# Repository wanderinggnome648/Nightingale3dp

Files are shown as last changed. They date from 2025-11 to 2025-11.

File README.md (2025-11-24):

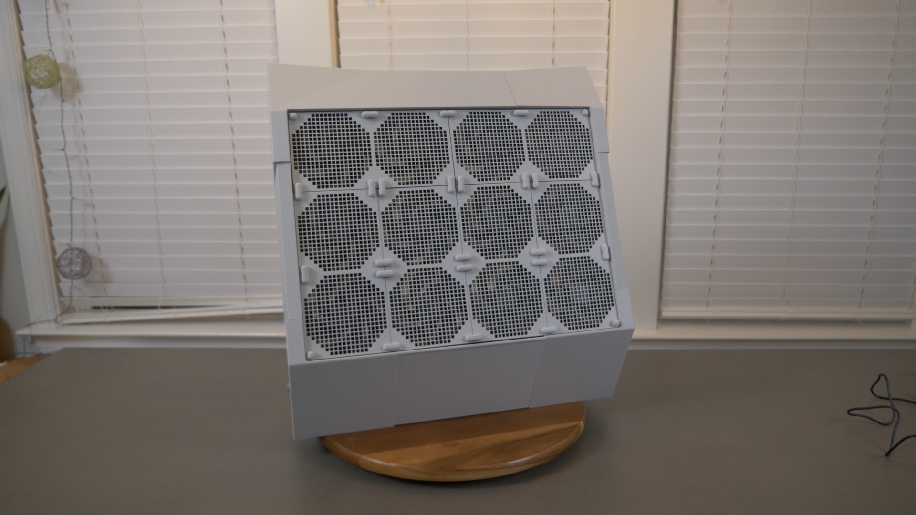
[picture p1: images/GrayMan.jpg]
Product image


# The Nightingale 3DP: An Open-Source, 3D Printed, Ultra-Quiet, Effective Air Purifier With Low Maintenance Costs

A PC-fan based air purifier design, the Nightingale's major features are:  
- **3D Printed**: Most parts are 3D printed, including the air purifier housing, fan grills, and connectors. You only need a filter, super glue, some wiring, and an A/C adapter.
- **Effective**: Purifies air with one 20x20x5 MERV 13 air filter is efficient at removing pollen, dust, and infectious aerosols, but have very high air flow.  
- **Ultra-Quiet**: No need to turn it down or off due to noise because you'll barely know it's running. Uses PC fans designed to push a high volume of air quietly. 
- **Easy Filter Change**: When you change the filters simply open the lid and replace. No disassembly required.
- **Cheap Maintenance**: No pricey filter replacement costs. Simply use standard MERV 13, 20x20x5 furnace filters commonly available in the US at $35-$40. Change yearly or after wildfire events. 
- **Open-Source**: No vendor lock-in. Build it. It's yours. If you have a problem, fix it. 
- **Low Energy Consumption** Consumes only enough electricity for 12 PC fans. 
- **Slim Design**: About the size of a desktop computer, it doesn't take up much space. Sit against the wall, and due to the angled design, it will still have good airflow. Air flow angles up slighty to help room mixing. 
- **Easy Wiring**: Uses standard connectors interior connectors (DC) that plug together. No soldering required.  

# Release Notes

## Version 1 - Baseline
Released on Nov 24, 2025. 

## 3D Printed Components
- Print all the items in the Nightingale_3d_7percent.3mf file with 2 Wall Loops, 7% Gyroid fill (to save on filament)
- Print all the items in the Nightingale_3d_30percent.3mf file with 2 Wall Loops, 30% Gyroid fill (for additional strength)
- You should be able to print all components with less then 3 rolls of filament. 
- You need cable ties for the wiring and those can also be printed. 

## Parts to Buy
| Quantity | Item | Description | Cost | Link  |
| --- | -----| --- | ---- | ----- |
| 1 | DC Barrel Jack | Used to easily connect to ac/dc adapter | $8 | 
| 1 | 12 volt, 4 amp AC/DC Adapter | Power source | $10 | [LINK](https://www.amazon.com/Converter-100-220V-Transformer-5-5x2-1mm-Accessories/dp/B08C594VNP/?th=1)
| 1 | 3 Way PWM Splitter | The splits 1 cable into 3 | $3 | [LINK](https://www.amazon.com/Splitter-Converter-Extension-Splitters-Computer/dp/B0DS2CVYZJ) (3-pack)
| 2 | 5-Port PWM Hubs | This connects multiple fans to power | $13 | [LINK](https://www.amazon.com/dp/B0CY521W9R/)
| 12 | P12 (120mm) PC Fans | Ideally, fluid bearings and advertised as quiet, Artic P12 is a solid inexpensive options | $68 | 2x [LINK](https://www.amazon.com/dp/B07HC7P3HJ/), 2x [LINK](https://www.amazon.com/ARCTIC-P12-120-Pressure-optimised-Quiet-Computer/dp/B07GB16RK7)
| 1 | MERV 13 20x20x5 Furnace Filter | Main filter for the unit | $45 | [LINK](https://www.nordicpure.com/product/20x20x5-air-filter/ ) |

Note: 20x20 furnace filters are NOT 20" long. They are always a little smaller. I designed this purifier to fit a filter with NordicPure sizing and some additional space for variances. 

## Other Parts and Tools
- Screwdriver - Connecting the fans to the panels
- Rubber mallet - Helps get stuff to fit snugly w/o damaging it
- Wood Glue - For affixing the filter holders
- Utility knife - Cutting zip ties, opening packages
- Cable ties - Organizing the wiring

# Assembly
[AssemblyVideo](https://youtu.be/DHxAwtPqRJc)

## Parts 
- Main body parts: M1, M2A, M2B, M3, M4, M5, M6, M7, M8
- Lid parts: L1, L2, L3
- Lots of: Pyramidal pins
- 48x Fan-through-rods
- 25x Dual rod connector
- 4x Single rod cover 
- 6x 2-Up fan grills

## Steps 
(Coming)

## FAQs

### Q: Why buy this instead of HEPA? 

- A: A HEPA filter is originally based on [World War II gas masks](https://en.wikipedia.org/wiki/HEPA), which explains the high efficiency. However, the high efficiency/low airflow is a disadvantage when purifying a room. HEPA purifiers tend to be big, loud, and have costly filter replacements. Furnace filter-based designs that use PC fans are an amazing combination of quiet and highly effective. 

### Q: What's the ideal environment for this design?

- A: I designed this as the purifier I would want in my kid's classroom. It can't be loud. And I don't want teachers to worry about turning it off/on or changing the speed settings. Finally, I wanted it to be durable, easy to fix if a component breaks, and easy to replace the filters. 

### Q: Why is it named 'The Nightingale'? 

- A: [Florence Nightingale](https://en.wikipedia.org/wiki/Florence_Nightingale) (1820-1910) was an activist, statistician, and the founder of modern Nursing. In her book, [*Notes on Nursing: What It Is, and What It Is Not*](https://archive.org/details/notesnursingwhat00nigh/page/6/mode/2up), she writes: 

> The very first canon of nursing, the first and the last thing upon which a nurse's attention must be fixed, the first essential to the patient, without which all the rest you can do for him is as nothing, with which I had almost said you may leave all the rest alone, is this: **TO KEEP THE AIR HE BREATHES AS PURE AS THE EXTERNAL AIR, WITHOUT CHILLING HIM.** 

### Q: What is the clean air delivery rate (CADR) of this unit? 

- A: I haven't had it officially tested by a reputable third party. Having 12 P12 Artic PC fans and a 20x20x5" filter, my best estimate is in the 300's for CADR. 

## Future Directions

## Acknowledgements

- [Corsi-Rosenthal Box](https://en.wikipedia.org/wiki/Corsi%E2%80%93Rosenthal_Box): In 2020, Corsi and Rosenthal popularized a simple DIY air purifier for removing airborne infectious disease using a box fan, furnace filters, and duct tape. At the time, the idea that a MERV 13 furnace filter, which has only [85% efficiency with tiny particles](https://www.ncbi.nlm.nih.gov/pmc/articles/PMC7127325/) could be better than HEPA filtration which has 99.99% efficiency seemed controversial. However, the key insight was that MERV 13 furnace filters had much better airflow than HEPA filters, which meant the total amount of clean air was much more. Disadvantages of the CR Box was only that it takes up space, the box fan can be louder than ideal for a classroom, and it's a temporary solution made with duct tape and is not extremely sturdy. [The Corsi-Rosenthal Foundation](https://corsirosenthalfoundation.org/) is a non-profit dedicated to promoting clean air and provides support to related charitable projects. 

- [Nukit Tempest](https://cybernightmarket.com/products/the-nukit-tempest-air-purifier-kit): An innovative and durable DIY air purifier design, the Tempest is made of metal and highly resembles a PC case. It's sleek and black, the six P14 fans are mounted inside, and it also takes 20x20x2 furnace filters. Overall, a near perfect design. Its only weaknesses are that you need to slightly disassemble the unit to replace the air filters, and you may not be able to tell that it's plugged in and running (because it's so quiet). Estimates are around 260-280 CFM. [A highly-recommended design](https://housefresh.com/nukit-tempest-review/) for situations where you want durable, simple, and ultra-quiet air cleaning. 

- [AirFanta Pro](https://www.amazon.com/AirFanta-based-Rosenthal-Purifier-3813ft2/dp/B0CJTYWQBT): Amazingly powerful and compact design using custom filters and PC fans, the 3Pro gets 430 CFM at full speed. It has a configurable adapter, which means if you don't mind the noise, you can crank it to max. However, if you want to limit the noise, you can lower the power. Importantly, this purifier is extremely portable -- you can pack it up inside a suitcase and take it with you. It's an absolute steal at <$200, especially considering the amazing cleaning power. I own several of these and enthusiastically recommend them to others. In particular, in schools where noise might not be as much of an issue (e.g., cafeteria, common areas), I think this is likely the best bang-for-the-buck. In classrooms, you can also purchase two of them and turn them to half speed.

- [CleanAirKits](https://www.cleanairkits.com/): The original DIY purifier kit builders, they offer many kit models with a lot of cleaning power using ultra-quiet PC fans. They've researched a ton of different PC fans and identified the good ones. I own several Tower of Power models and have recommended them often to friends. In fact, a luggable protects my dad when he's in the office meeting people.

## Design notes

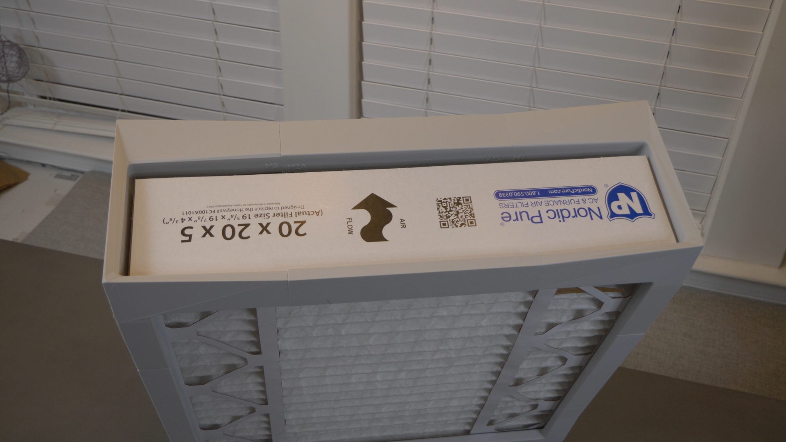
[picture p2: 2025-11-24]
images/FanShown.jpg

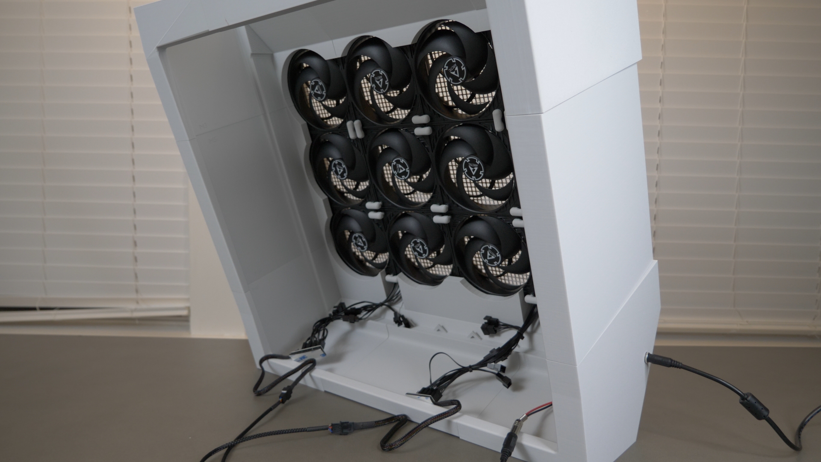
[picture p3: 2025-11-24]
images/Interior.jpg

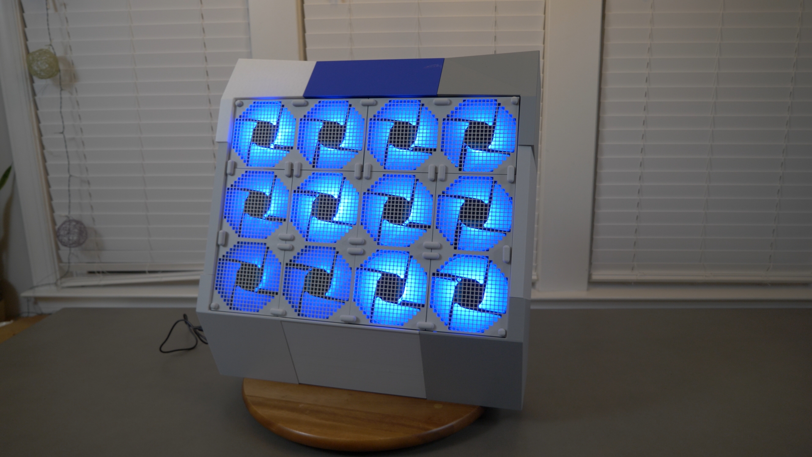
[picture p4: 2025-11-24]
images/LightUp2.jpg

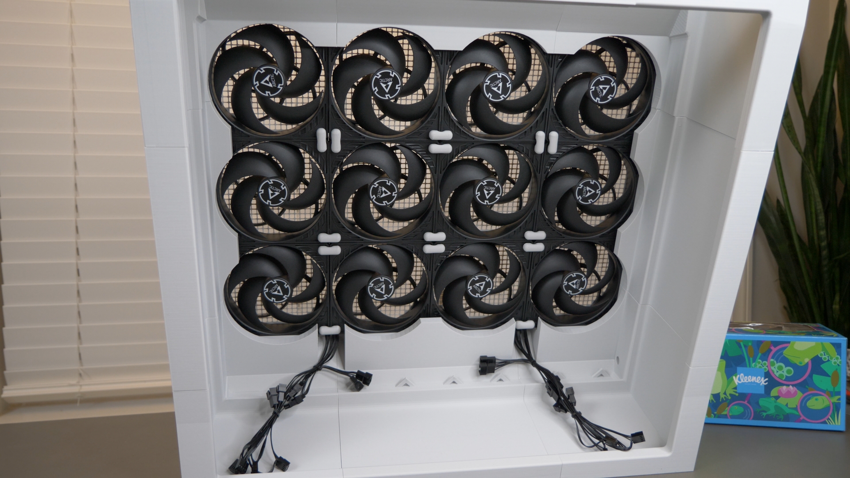
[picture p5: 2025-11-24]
images/FansPlaced.jpg

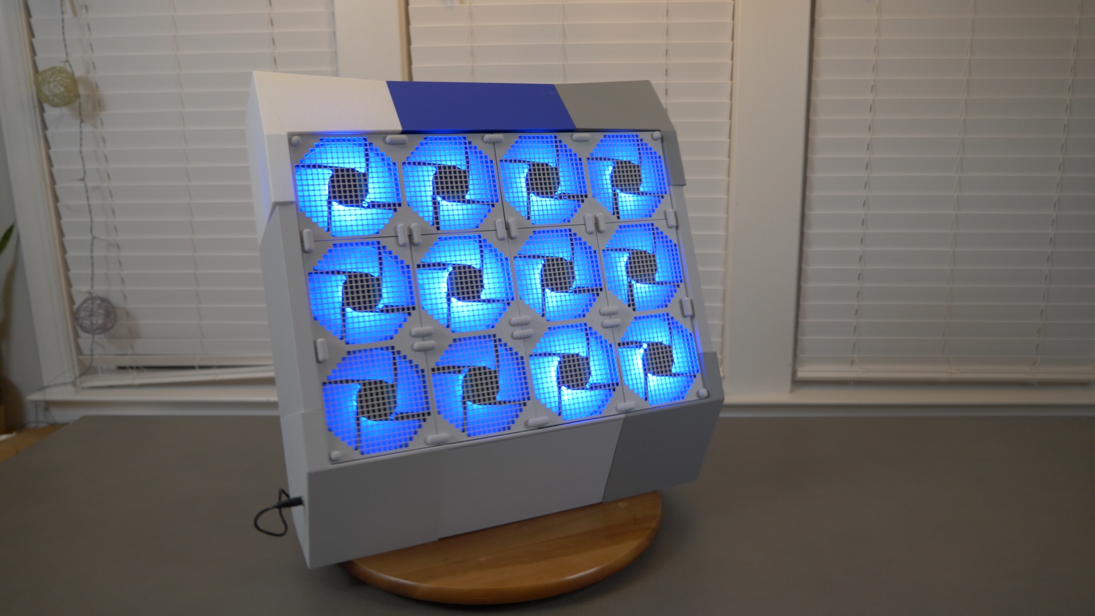
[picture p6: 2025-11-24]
images/LightUP.jpg

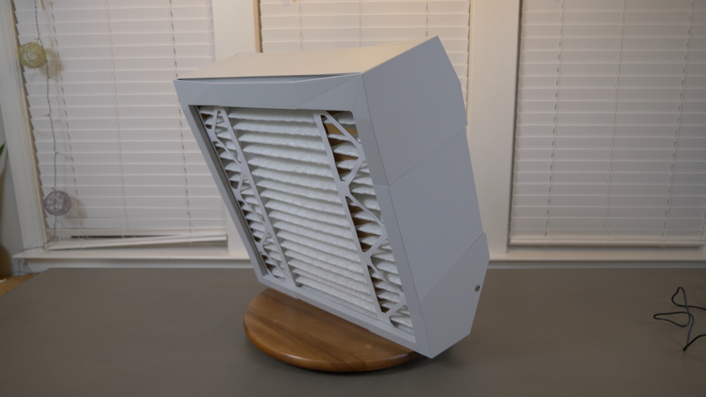
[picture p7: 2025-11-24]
images/GrayManBack.jpg

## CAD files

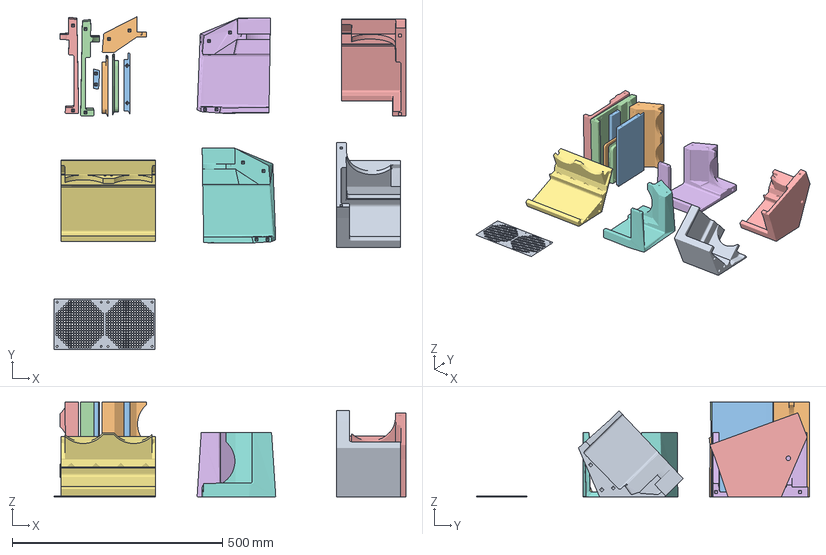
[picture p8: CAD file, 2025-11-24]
models/bambu/Nightingale_3d_7percent.3mf
835.7 x 791.3 x 225.1 mm
2x2FanGrill.stl
Main2A.stl
Main2B.stl
Main5.stl
Main4.stl
Main3.stl
Main7.stl
Main1.stl
Main8.stl
L3.stl
L2.stl
L1.stl
Main6.stl

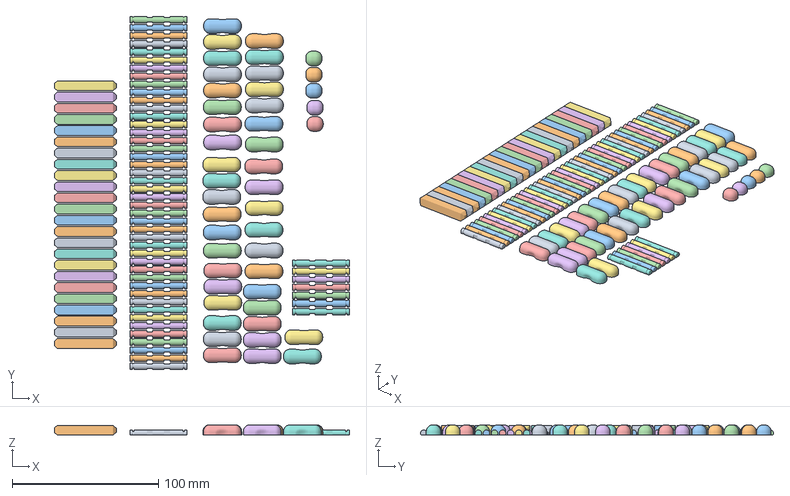
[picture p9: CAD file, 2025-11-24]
models/bambu/Nightingale_3d_30percent.3mf
201.5 x 241.0 x 6.97 mm
LockDimple.stl x 40
Lock1.stl x 5
Pin95FlatEnd.stl x 24
Pole.stl x 51

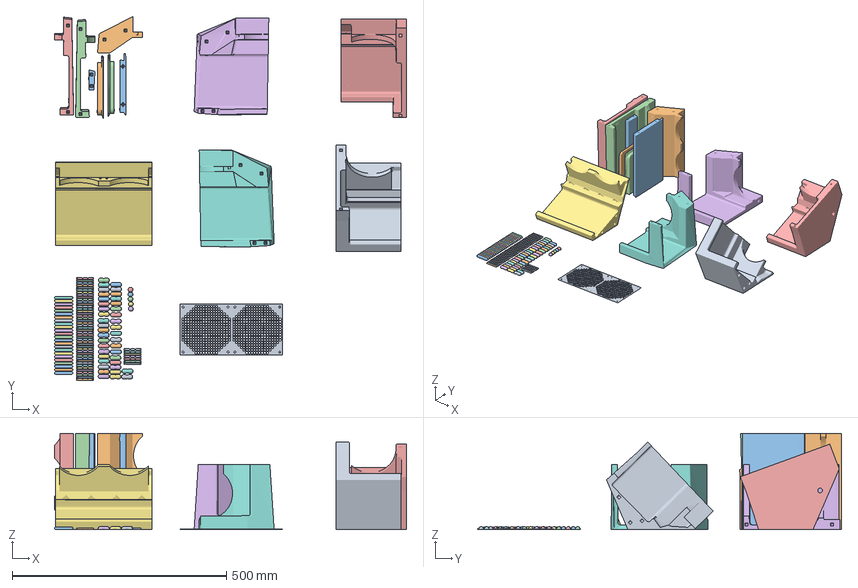
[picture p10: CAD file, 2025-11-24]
models/bambu/Nightingale_3d_all_items.3mf
822.0 x 850.6 x 225.1 mm
2x2FanGrill.stl
LockDimple.stl x 40
Lock1.stl x 5
Pin95FlatEnd.stl x 24
Pole.stl x 51
Main2A.stl
Main2B.stl
Main5.stl
Main4.stl
Main3.stl
Main7.stl
Main1.stl
Main8.stl
L3.stl
L2.stl
L1.stl
Main6.stl

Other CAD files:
models/blender/nightgale3dp_sliced.blend
